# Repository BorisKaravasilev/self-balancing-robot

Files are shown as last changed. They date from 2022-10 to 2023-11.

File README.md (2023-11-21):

# Self Balancing Robot

*ITU - Summer 2022 - How to Make (almost) Anything*

**Team members:**

- Anders Latif
- Boris Karavasilev
- Stefan Bjerring Henriksen

The full report can be found [here](./report.pdf).

## Introduction

During my master's degree in the summer of 2022, I took the most fun course of my life called "How to Make (almost) Anything". I loved it because it was cross-disciplinary and combined software with hardware. In this course, me and my two friends built a self-balancing robot. We implemented and calibrated a PID controller on an Arduino. We also designed the entire body of the robot in Fusion 360 and used a combination of 3D printing and laser cutting to manufacture the robot. We tested the robot in various conditions and documented the results in a report.

## Design Brought To Reality

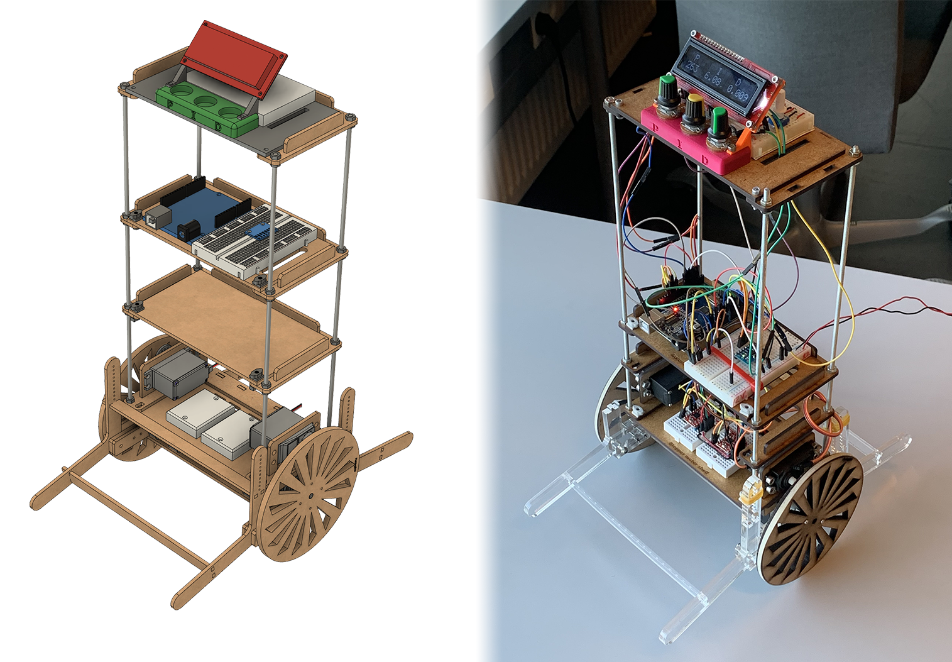
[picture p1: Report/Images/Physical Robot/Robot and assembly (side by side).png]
design vs. reality


## Video
👇 To see our robot in action click on the image below. 👇

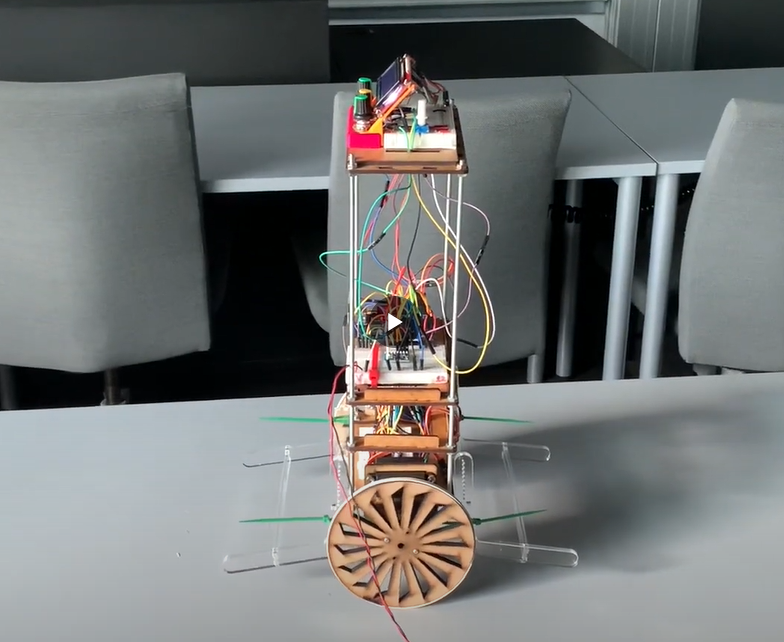
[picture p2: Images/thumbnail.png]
(https://youtu.be/ohNkID8hXRA)


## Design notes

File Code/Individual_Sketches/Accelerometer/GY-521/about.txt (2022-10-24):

The GY-521 is a accelerometer, gyroscope and temperature reader

Fritzing file provided from:
https://create.arduino.cc/projecthub/Nicholas_N/how-to-use-the-accelerometer-gyroscope-gy-521-6dfc19

Really good explenations of the code:
https://www.youtube.com/watch?v=y5X2zwbO6e4&t=1298s

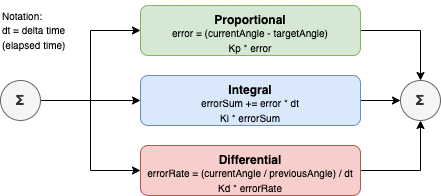
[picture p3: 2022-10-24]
Report/Images/PID_Control_General_Diagram.png

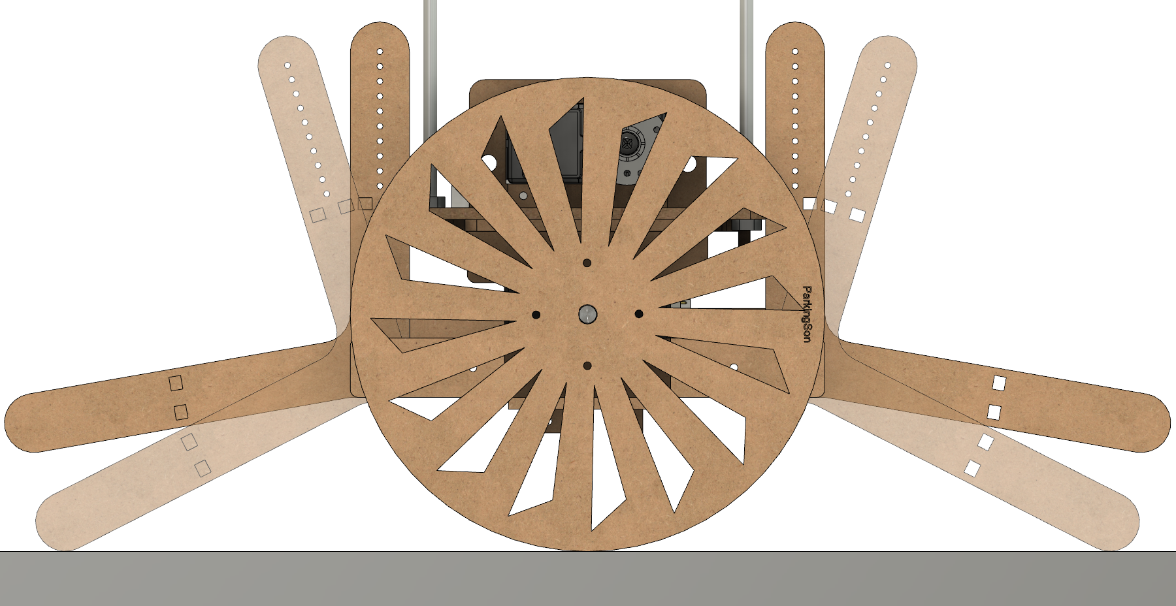
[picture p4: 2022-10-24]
Report/Images/Legs/legs-up-down.png

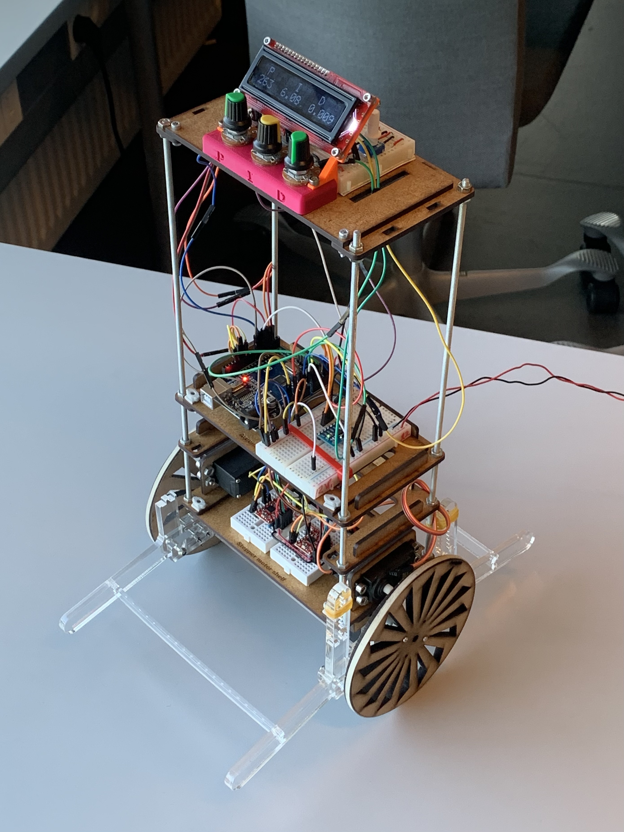
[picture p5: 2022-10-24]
Report/Images/Physical Robot/Physical Robot.jpg

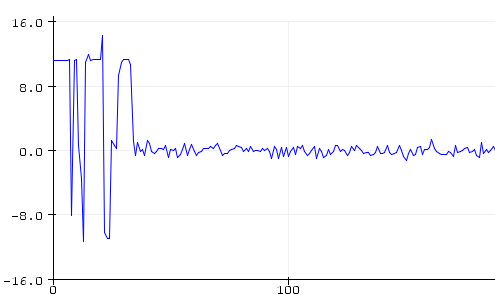
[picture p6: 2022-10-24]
Report/Images/PID/PID error plot.png

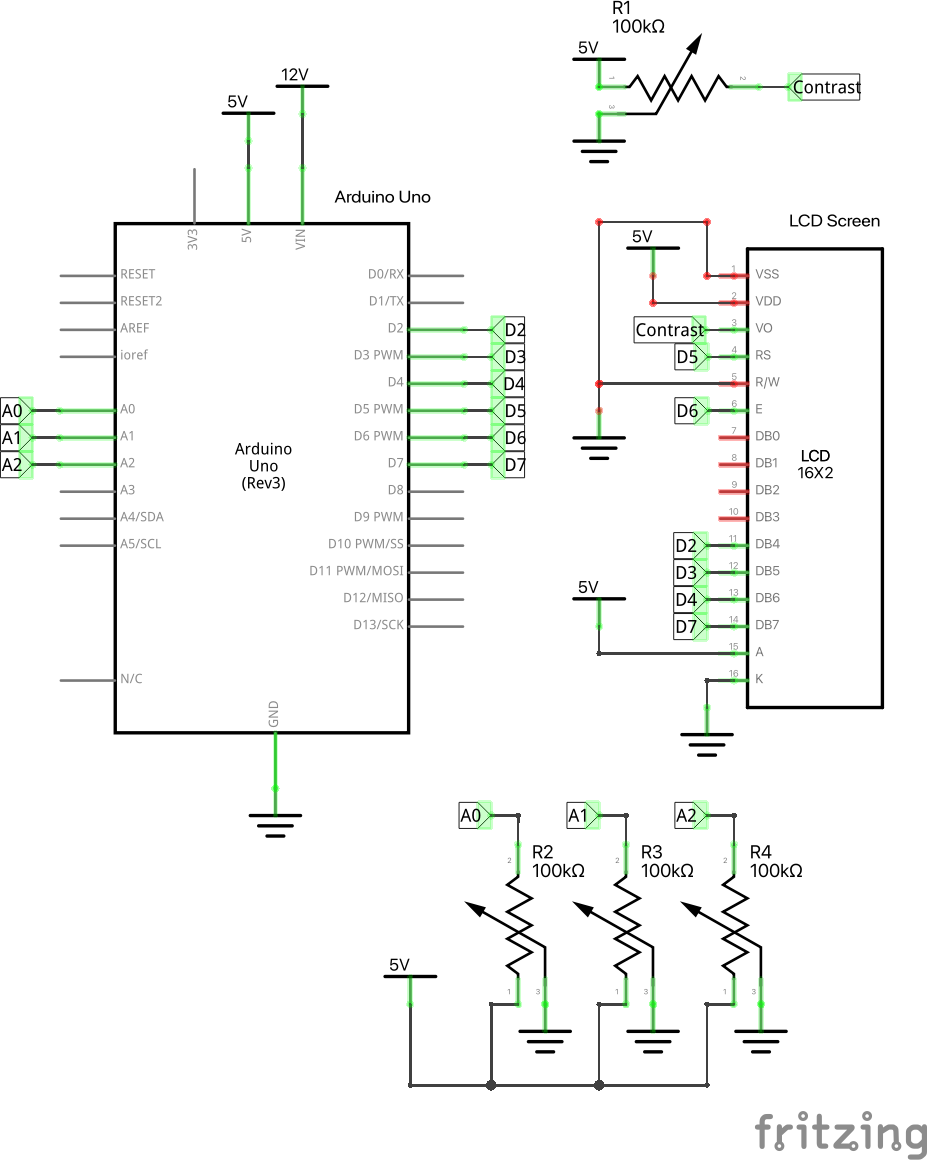
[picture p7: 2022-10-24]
Fritzing/PID Tweaker Schematic.png

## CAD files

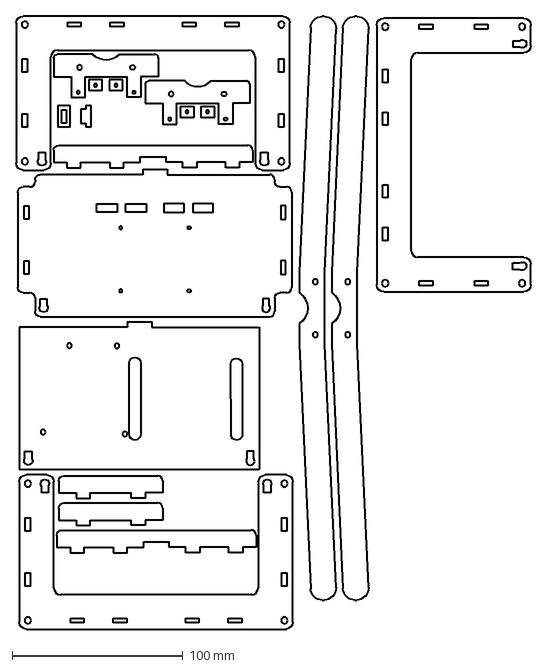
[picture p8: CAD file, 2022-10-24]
Design/Motor Shelf + Arduino Shelf + Training Wheels + Holders (laser cutting drawing).dxf
301.1 x 358.8 mm

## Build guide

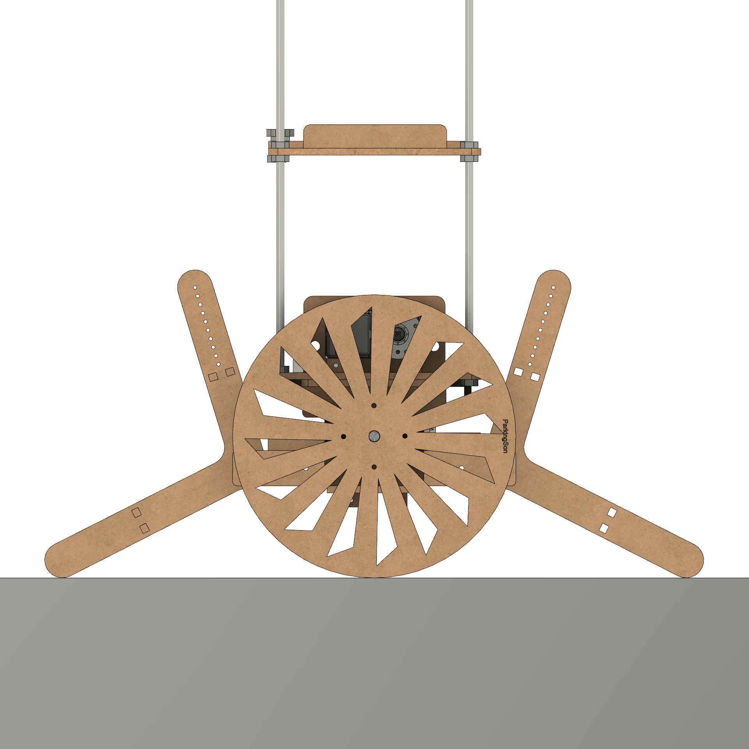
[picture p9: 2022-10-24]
Report/Images/Legs/Balancing Robot Assembly v23 2 (Legs down).png

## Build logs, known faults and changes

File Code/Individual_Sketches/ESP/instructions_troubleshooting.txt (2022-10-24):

Note: Ours is the XC4411. 

On getting the following error when compiling:
> esp_client_server:1:10: fatal error: ESP8266WiFi.h: No such file or directory
Choose the right board (Generic ESP8266)

If you haven't already, install the ESP8266 Boards addon as per the XC3802
manual located on the product page:

https://jaycar.com.au/p/XC3802

the code in this zipfile is used as an example for our new XC4421 and XC4411
boards.

To write arduino code: 
-------------------------------------
Configure the dip switches as shown: 3,4 are on, the others are off.

|-|-|o|o|-|-|-|-| on
|o|o|-|-|o|o|o|o| off
|1|2|3|4|5|6|7|8|

for XC4421 select Tools->Board->Arduino Mega (for XC4421) Or Uno (for XC4411)

open arduino.ino and press upload.

To write esp code:
-------------------------------------
Configure the dip switches as shown: 5,6,7 are on, the others are off.

|-|-|-|-|o|o|o|-| on
|o|o|o|o|-|-|-|o| off
|1|2|3|4|5|6|7|8|

for XC4421 select Tools->Board->Generic 8266 Module
-> If you cannot see it, you did not read the XC3802 Manual!

open esp.ino and press upload; after compiling, when the IDE says "Uploading.."
You should begin to see ".......________........_____" during this time, press 
the reset button on the MCU; the ESP should begin to accept
instructions.

To run the example:
---------------------------------------
Upload both of the code as above, then configure the switches as shown: (1,2 are on)

|o|o|-|-|-|-|-|-| on
|-|-|o|o|o|o|o|o| off
|1|2|3|4|5|6|7|8|

Open up your wireless internet and you should see a new wireless network.
Connect to it and navigate to http://10.0.0.7, you'll see two hyperlinks
to turn the arduino L13 led on/off. You should be able to see the device
interplay between your phone/computer, the ESP, and the arduino.

Troubleshooting:
-----------------------------------------

"upload esp mem failed" in arduino IDE ESP8266 error:
	* have you selected the right switch config? ensure that 5,6, AND 7, are
	  switched _ON_
	* Did you press the MCU Reset button when the IDE says "uploading" ?

"WiFiServer.h not found" or similar not found messages
	* Did you install the ESP8266 Boards in the Arduino IDE? read the XC3802
	  manual.
	* Have you selected the right board for the project? make sure
	  Tools->Board->Generic8266 board is selected for the ESP project, and
	  Geniuno is selected for Arduino 

Writing html code is better in proper html files, which can be stored in a "data" folder
and uploaded automatically, check out "SPIFFS" for more information:

https://randomnerdtutorials.com/esp8266-web-server-spiffs-nodemcu/

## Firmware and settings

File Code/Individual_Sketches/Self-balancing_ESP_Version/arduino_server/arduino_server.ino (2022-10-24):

// Standard libraries
#include <Wire.h>
#include <LiquidCrystal.h>
#include <Servo.h>

// Our files


/* Include the AccelStepper Library
(search in the library manager "accelstepper")
Library docs: http://www.airspayce.com/mikem/arduino/AccelStepper/ */
#include <AccelStepper.h>

/* From I2Cdev install zip the following 2 folders under Arduino and install them through the IDE
https://github.com/jrowberg/i2cdevlib

 1) Download the ZIP from GitHub
 2) Go to "i2cdevlib-master.zip > i2cdevlib-master > Arduino"
 3) Zip "I2Cdev" and "MPU6050" into individual zip archives
 4) Include them one by one through the Arduino IDE
      -->  "Sketch > Include Library > Add .ZIP Library..."
*/
#include "I2Cdev.h"
#include "MPU6050.h"


//**************************************************************
// GLOBAL VARIABLES
//**************************************************************

/*
 * Fine tuning the PID constants
1. Set Ki and Kd to zero and gradually increase Kp so that the robot starts to oscillate about the zero position.

2. Increase Ki so that the response of the robot is faster when it is out of balance. 
Ki should be large enough so that the angle of inclination does not increase. 
The robot should come back to zero position if it is inclined.

3. Increase Kd so as to reduce the oscillations. The overshoots should also be reduced by now.

4. Repeat the above steps by fine tuning each parameter to achieve the best result.
*/
float Kp = 150; //100;
float Ki = 5.1; // Influence of the sum of integrated errors in the final equation
float Kd = 0;

const float SPEED_OF_INTEGRATION = 460; // Multiplier of the integrated error
const float MAX_INTEGRATION_SUM = 70; // Floor and ceiling in order to make it easier to go back to zero sum
                                       // (to not be too far in the positive or negative numbers)


// Define how often code in inner loop should run
const int loopMax = 1000;
int loopCounter = loopMax;



//**************************************************************
// Stepper motor variables
//**************************************************************

// Define motor interface type
#define motorInterfaceType 1

const int MOTOR_MAX_SPEED = 1000;

// PIN CONNECTIONS
const int M1_DIR_PIN = 11; 
const int M1_STEP_PIN = 10;

const int M2_DIR_PIN = 12; // 8 to 13
const int M2_STEP_PIN = 13; // 9 to 13

// LCD Data Pins

const int LCD_d_4 = 2;
const int LCD_d_5 = 3;
const int LCD_d_6 = 4;
const int LCD_d_7 = 7;

const int LCD_Register_Sel = 5;
const int LCD_Enable = 6;

// Creates an instance
AccelStepper stepper1(motorInterfaceType, M1_STEP_PIN, M1_DIR_PIN);
AccelStepper stepper2(motorInterfaceType, M2_STEP_PIN, M2_DIR_PIN);


//**************************************************************
// LCD Screen
//**************************************************************

// Setup LCD pins to Arduino pins
LiquidCrystal lcd(LCD_Register_Sel, 
                  LCD_Enable, 
                  LCD_d_4, 
                  LCD_d_5, 
                  LCD_d_6, 
                  LCD_d_7);

// Ranges for PID tweak values
// Change these when testing
float KpMin = 50;
float KpMax = 200;

float KiMin = 0;
float KiMax = 120;

float KdMin = 0;
float KdMax = 0.01;

// Maximum analog read value for our arduino
const int PotMax = 1023;

const float KpFactor = (KpMax - KpMin) / PotMax;
const float KiFactor = (KiMax - KiMin) / PotMax;
const float KdFactor = (KdMax - KdMin) / PotMax;

// The readings from the potentiometers
int KpRead = 0;
int KiRead = 0;
int KdRead = 0;

// PID Tweaker pins
const int TWEAK_KP_PIN = A0;
const int TWEAK_KI_PIN = A1;
const int TWEAK_KD_PIN = A2;



//**************************************************************
// MPU6050 variables = Accelerometer + Gyroscope 
//**************************************************************
MPU6050 mpu;

/* MPU */
int16_t AcY, AcZ, GyX;


//**************************************************************
// PID variables
//**************************************************************

/* MOTOR */
volatile int motorPower, gyroRate;

/* PID */
volatile float accAngle, gyroAngle, currentAngle, prevAngle=0, error, prevError=0, errorSum=0, errorRate=0;

const float targetAngle = -12.22;
/* This is assuming that it is in a forward resting position on the support wheels. If leaning back then change the sign.
 *  Code for recalculating the target angle
 *    float sum = 0;
  float readings = 20000;
  for (int i = 0; i < readings; i++) {
      AcY = mpu.getAccelerationY();
      AcZ = mpu.getAccelerationZ(); 
      sum += atan2(AcY, AcZ)*RAD_TO_DEG;
  }
  Serial.println(sum / readings);
 */

unsigned long prevTimePID;
unsigned long currentTimePID;
float elapsedTimePIDSeconds;

//**************************************************************
// Servos - Legs
//**************************************************************

// One leg on each side share the same pins
const int SERVO_LEFT_LEG_PIN = 8; // todo change to the right pin
const int SERVO_RIGHT_LEG_PIN = 9; // todo change to the right pin
//LegsStepper rightLeg;
//LegsStepper leftLeg;
Servo rightLeg;
Servo leftLeg;

//**************************************************************
// SETUP
//**************************************************************
void setup() {
  Serial.begin(9600);
  
  // ******** Stepper Motor
  stepper1.setMaxSpeed(MOTOR_MAX_SPEED);
  stepper2.setMaxSpeed(MOTOR_MAX_SPEED);
  stepper1.setSpeed(0);
  stepper2.setSpeed(0);

  // ******** Leg Servos
//  rightLeg.initialize(SERVO_RIGHT_LEG_PIN);
//  leftLeg.initialize(SERVO_LEFT_LEG_PIN);
  rightLeg.attach(SERVO_RIGHT_LEG_PIN);

  // ******** LCD - Welcome Screen
  // Setup the first (unchanging) line of the display
  lcd.begin(16, 2);
  lcd.setCursor(0, 0);
  lcd.print("Callibrating...");
  lcd.setCursor(0, 1);
  lcd.print("PS Loves You");

  // this is because turning on the power supply jolts the motors and this interfers with the mpu callibration. 
  delay(400);

  // ******** MPU
  mpu.initialize();
  // todo raise the value when done developing
  mpu.CalibrateAccel(8);
  mpu.CalibrateGyro(8);

  // ******** LCD - Info Screen
  lcd.setCursor(0, 0);
  lcd.print(" P     I    D  ");
  lcd.setCursor(0, 1);
  lcd.print("               ");

  // ******** PID
  prevTimePID = millis();
 
}

//**************************************************************
// LOOP
//**************************************************************
void loop() {
  AcY = mpu.getAccelerationY();
  AcZ = mpu.getAccelerationZ();  
  GyX = mpu.getRotationX();
  
  calculatePID();

  stepper1.setSpeed(motorPower);
  stepper2.setSpeed(-motorPower); // inverted speed because motors are facing opposite directions
  
  stepper1.runSpeed();
  stepper2.runSpeed();
 
  if (loopCounter < loopMax) {
      loopCounter++;
    } else {
      loopCounter = 0;
      updatePIDValuesFromTweaker();
      showPIDValuesOnScreen();
  }

  /* ESP CODE === NEW */
  // since this is not in a while loop constantly receiving it might miss the entire command
  if (Serial.available()) {
    handleClientCommands();
  }
}


void calculatePID() {
  currentTimePID = millis();
  elapsedTimePIDSeconds = (currentTimePID - prevTimePID) / 1000.0f;

  accAngle = atan2(AcY, AcZ)*RAD_TO_DEG;

  // The MPU6050 outputs values in a format in a range that needs to be converted
  gyroRate = map(GyX, -32768, 32767, -250, 250);
  gyroAngle = (float) gyroRate * (elapsedTimePIDSeconds);


  // even the angle out by adding to the previous angle
  // this is the formula for the complementary filter
  // Page 11: https://d1.amobbs.com/bbs_upload782111/files_44/ourdev_665531S2JZG6.pdf 
  currentAngle = 0.98 * (prevAngle + gyroAngle) + 0.02 * (accAngle);

  error = currentAngle - targetAngle;
  errorSum += SPEED_OF_INTEGRATION * error * elapsedTimePIDSeconds;

  errorSum = constrain(errorSum, -MAX_INTEGRATION_SUM, MAX_INTEGRATION_SUM);

  errorRate = (currentAngle-prevAngle)/elapsedTimePIDSeconds;
  
  // calculate output from P, I and D values
  motorPower = Kp*error + Ki*errorSum - Kd*errorRate;
  motorPower = constrain(motorPower, -MOTOR_MAX_SPEED, MOTOR_MAX_SPEED);
  
  
  prevAngle = currentAngle;
  prevTimePID = currentTimePID;
}

void updatePIDValuesFromTweaker() {

  // Find the proportional, update the value and write to LCD
  KpRead = PotMax - analogRead(TWEAK_KP_PIN);
  Kp = KpRead * KpFactor + KpMin;


  // Find the integral, update the value and write to LCD
  KiRead = PotMax - analogRead(TWEAK_KI_PIN);
  Ki = KiRead * KiFactor + KiMin;


  // Find the derivative, update the value and write to LCD
  KdRead = PotMax - analogRead(TWEAK_KD_PIN);
  Kd = KdRead * KdFactor + KdMin;

}

void showPIDValuesOnScreen() {
  lcd.setCursor(0, 1);
  lcd.print(Kp);
  
  lcd.setCursor(6, 1);
  lcd.print(Ki);
  
  lcd.setCursor(12, 1);
  lcd.print(Kd);
}

void moveLegUp(Servo servo) {
  servo.write(180);
}

void moveLegDown(Servo servo) {
  servo.write(0);
}

/* ESP CODE === NEW */
String receivedCommand = "";
bool dataIn = false;

void handleClientCommands() {
  while (Serial.available()) {
		char c = Serial.read(); //read it

		if (c == '[') {
			// this is the start of the command string
			receivedCommand = "";
			dataIn = true;
		}
		// otherwise, we are still reading the command string:
		else if (dataIn && c != ']'){
			receivedCommand += c;
		}

		else if (dataIn && c == ']') {
			//finished receiving the command, process it

			if (receivedCommand == "DELAY"){
        delay(10000);
			}
		}
	}
}

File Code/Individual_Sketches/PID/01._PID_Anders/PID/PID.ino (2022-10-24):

#include <Wire.h>

/* MPU */
const int MPU = 0x68; // I2C address of the MPU-6050
//int16_t AcX, AcY, AcZ, Tmp, GyX, GyY, GyZ;
int16_t tilt_y, AcY, AcZ, Tmp, GyX, GyY, GyZ;

const int TILT_RANGE = 16000; // 0 - 16 000 (corresponds to approx. 0 - 90°)

/* MOTOR */
volatile int motorPower, gyroRate;

/* PID */
volatile float accAngle, gyroAngle, currentAngle, prevAngle=0, error, prevError=0, errorSum=0;

const int Kp = 40;
const int Ki = 40;
const int Kd = 0.05;
const float targetAngle = -2.5;

long prevTimePID;
long currentTimePID;
float elapsedTimeSecondsPID;

void setup() {
  setupMPU();
  
  Serial.begin(9600);

  initializePID();

  prevTimePID = millis();
}

void setupMPU() {
  Wire.begin();
  Wire.beginTransmission(MPU);
  Wire.write(0x6B); // accessing the PWR_MGMT_1 register
  Wire.write(0);   // set to zero wakes up the MPU-6050 
                   // goes straight to sleep mode after being woken up thus the two step begin transmission in the loop
  Wire.endTransmission(true);
}

void initializePID() {

}


void loop() {
  read_accelerometer();

  

  calculatePID();

  Serial.println(motorPower);

}

// ISR (Interrupt Service Routine) is a function that will be called every 5 miliseconds
// TIMER1_COMPA_vect is a library constant that needs to be given
// ISR(TIMER1_COMPA_vect) {}

void calculatePID() {
  accAngle = atan2(AcY, AcZ)*RAD_TO_DEG;
  
  // convert it gyro around x to degrees per second and then multiply it with the loop time to obtain the change in angle
  gyroRate = map(GyX, -32768, 32767, -250, 250);

  currentTimePID = millis();
  elapsedTimeSecondsPID = (currentTimePID - prevTimePID) / 1000;
  prevTimePID = currentTimePID;
  
  gyroAngle = (float) gyroRate * (elapsedTimeSecondsPID);

  // even the angle out by adding to the previous angle
  // the magic numbers are part of the equation for the complementary filter
  currentAngle = 0.9934 * (prevAngle + gyroAngle) + 0.0066 * (accAngle);

  error = currentAngle - targetAngle;
  errorSum = errorSum + error;  
  errorSum = constrain(errorSum, -300, 300);

  // calculate output from P, I and D values
  motorPower = Kp*(error) + Ki*(errorSum)*elapsedTimeSecondsPID - Kd*(currentAngle-prevAngle)/elapsedTimeSecondsPID;
  motorPower = constrain(motorPower, -255, 255);
  
  prevAngle = currentAngle;
}

void motor_speed_tmp() {
  int motor_speed = 0;
  bool motor_dir = 0;

  if (tilt_y > 0){
    motor_speed = map(tilt_y, 0, TILT_RANGE, 0, 255);
    motor_dir = 0;
  } else {
    motor_speed = map(tilt_y, 0, -TILT_RANGE, 0, 255);
    motor_dir = 1;
  }
  
  Serial.print("Motor direction: "); Serial.println(motor_dir);
  Serial.print("Motor speed: "); Serial.println(motor_speed);
}

void read_accelerometer() {
  Wire.beginTransmission(MPU);
  Wire.write(0x3B);  
  Wire.endTransmission(false);
  Wire.requestFrom(MPU, 14, true);  // request a total of 14 register bytes from the MPU

  tilt_y = Wire.read()<<8|Wire.read();
  AcY = Wire.read()<<8|Wire.read();
  AcZ = Wire.read()<<8|Wire.read();
  Tmp = Wire.read()<<8|Wire.read(); // temperature to be discarded
  GyX = Wire.read()<<8|Wire.read();
  GyY = Wire.read()<<8|Wire.read();
  GyZ = Wire.read()<<8|Wire.read();
}
